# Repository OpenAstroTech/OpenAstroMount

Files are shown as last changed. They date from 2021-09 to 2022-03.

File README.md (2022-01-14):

# OpenAstroMount

OAM

v1.0 released now! 

The OpenAstroMount is a mount meant for larger telescopes that the OpenAstroTracker can't handle. It's fairly heavy and bulky, but can pack quite some payload. It features build in autoPA through motorized ALT and AZ axis. Both RA and DEC are driven entirely by belts, resulting in extremely low backlash. On both axis there is a two-stage belted gearbox with a reduction of 9:1 which, in combination with the large RA and DEC wheels, gives a total reduction of 316:1 and 234:1 for RA and DEC respectively. 

Specs:

| Weight | Cost | Payload | Performance (PHD2) |
|---|---|---|---|
| 12kg + tripod <br>& counterweights | ~300-500$ | 5+ kg* | 0.5-0.7" RMS |

`* since my heaviest gear weighs only about 4kg, i haven't tested the mount with more payload, hence the official payload recommendation remains 5kg. This will likely increase once the mount has been tested with more payload. ` 

---
### ToDo
- ~~AZ fine adjustment~~
- ~~ALT fine adjustment~~
- ~~RA/DEC gearboxes~~
- ~~cable managment~~
- ~~Place for MKS~~
- ~~Full BOM~~
- Guides
- Drill jigs

---
### Fix
- Misumi style extrusions do not fit parts
- ~~resize some holes~~
- ~~Base still too wobbly~~
- ~~RA Ring not printable on small printers~~
- ~~Some screws are very hard to reach~~
---
### Links
- [Guides](https://wiki.openastrotech.com/en/OpenAstroMount)
- [Shopping List](https://docs.google.com/spreadsheets/d/11bVmNJqMsgxGibqhDkgMZYvdXtIfOjpVwsbMoQk8eRM/edit?usp=sharing)
- [Printed parts list](https://docs.google.com/spreadsheets/d/1Y-b5y6xR6_xKHy6ZGzY7_cjVsc-U0AEJJASNaPWRuvU/edit?usp=sharing)

---
### Changelog:

see [changelog](https://github.com/OpenAstroTech/OpenAstroMount/blob/master/changelog.md)

---

<br /> <a href="https://github.com/OpenAstroTech/OpenAstroMount"> OpenAstroMount </a> &copy; 2021 by <a href="https://github.com/OpenAstroTech">OpenAstroTech </a> is licenced under <a rel="license" href="http://creativecommons.org/licenses/by-nc/4.0/">CC BY-NC 4.0</a>.

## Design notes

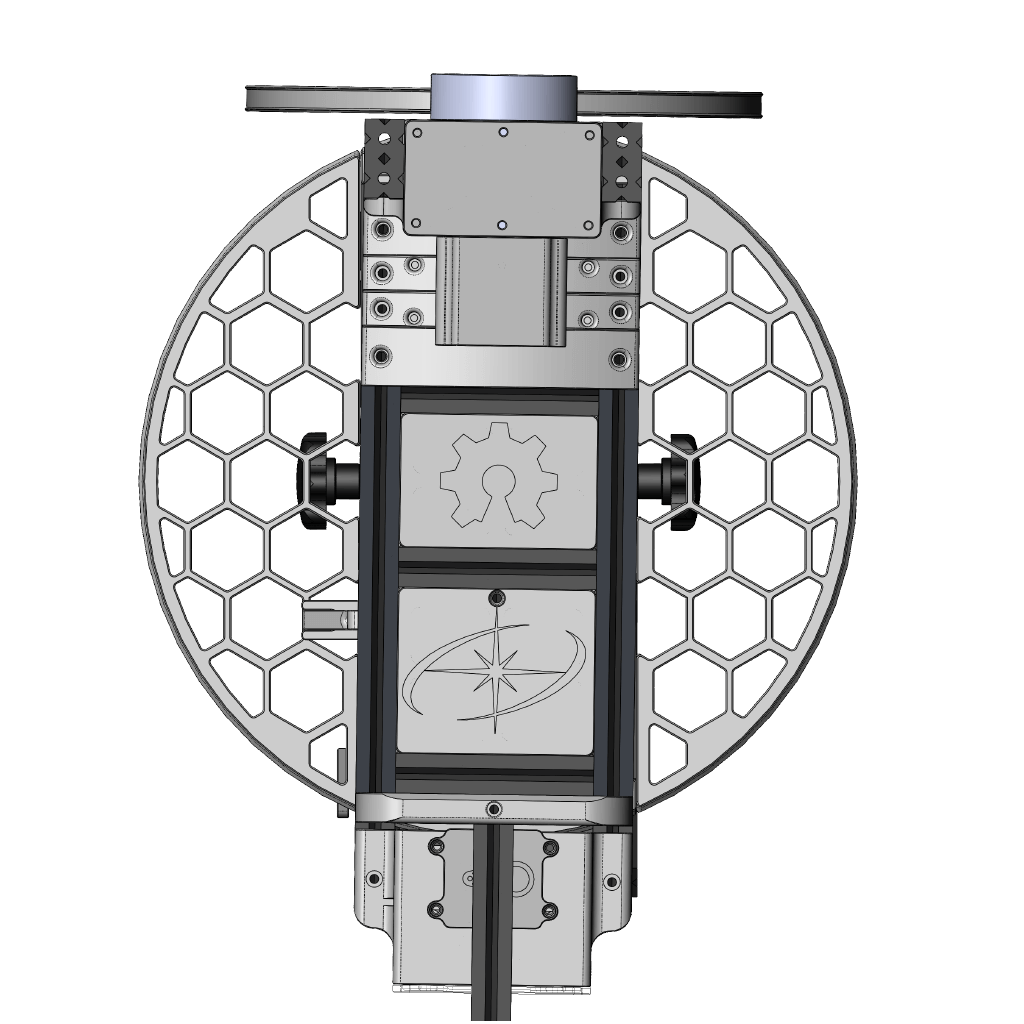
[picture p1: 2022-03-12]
CAD/Solidworks/OpenAstroMount_v1.0.PNG

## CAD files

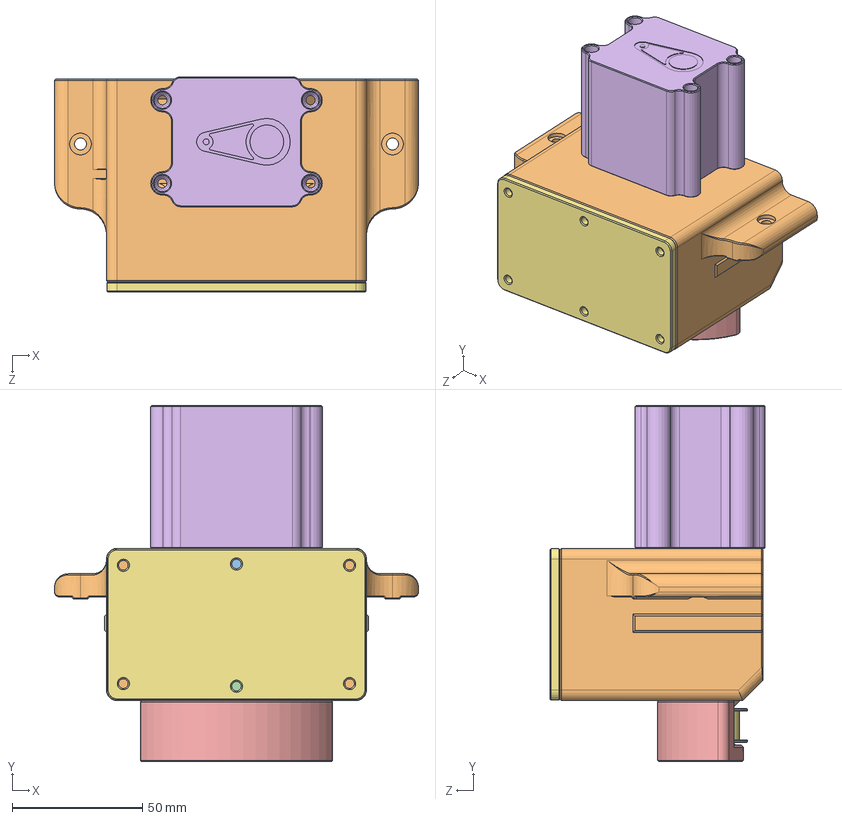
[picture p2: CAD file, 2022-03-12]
CAD/Solidworks/top_assembly/gearbox_v2/Gearbox_v2.SLDASM
140.0 x 137.0 x 82.8 mm
NEMA 17
GT2_16T x 2
GT2_16T_9mm
5x50mm rod x 2
625_bearing x 4
GT2_48T_8_6 x 2
GT2_idler_20T_toothless x 2
M5x30mm x 2
M5_nut x 2
gearbox_body_v2
Slider_top
Slider_bottom
pulley_cover
Stepper_cover
Lid

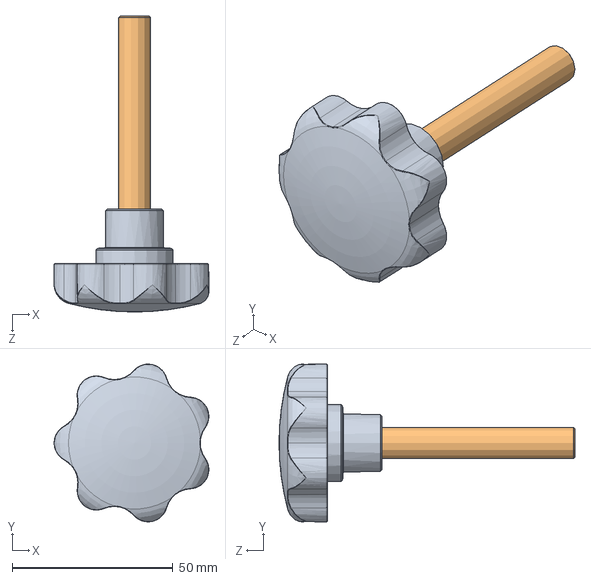
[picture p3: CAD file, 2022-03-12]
CAD/Solidworks/base_assembly/assembly_only/Star handle.stp.SLDASM
48.1 x 49.0 x 92.0 mm
Handle.stp
Bolt.stp

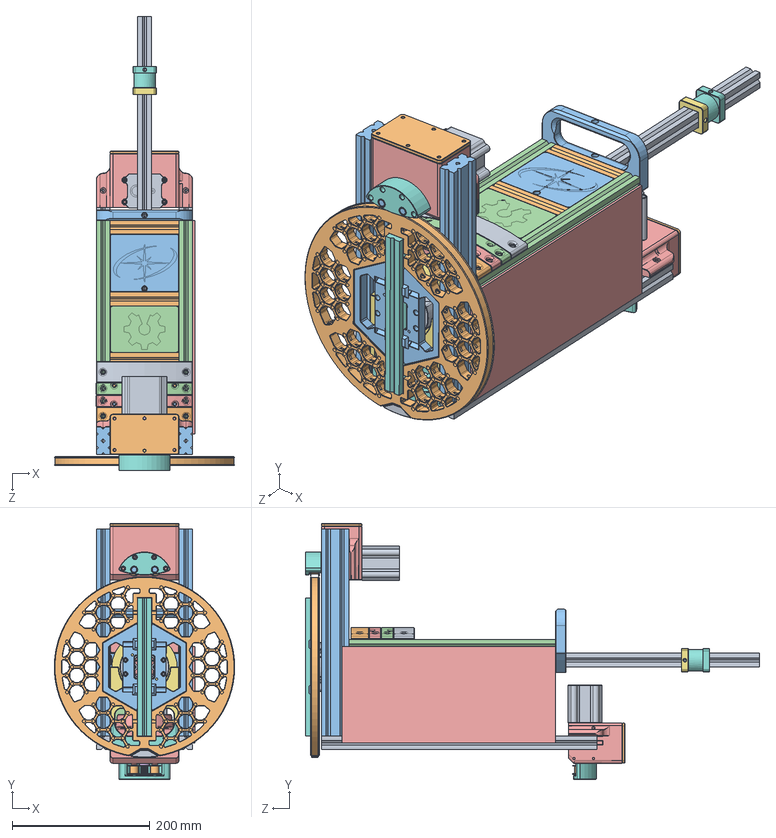
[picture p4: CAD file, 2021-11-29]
CAD/Solidworks/top_assembly/Top_Assembly.SLDASM
261.8 x 371.5 x 659.2 mm
2040 300mm x 2
Mancal F206 x 2
Rolamento UC206 x 2
6012 bearing x 2
4040_dual_slot
DEC_bearingHolder_rear_bottom
DEC_bearingHolder_front_bottom
DEC_bearingHolder_rear_top
DEC_bearingHolder_front_top
DECholder_1_v2
DECholder_2_v2
Baseplate_1_v1
top_cover
top_cover_2
Top_Plate_1
Top_Plate_2
MKS_enclosure
20x80x120
4040adapter_mid x 2
4040adapter_rear
4040adapter_front
DEC_wheel_2_v2
CW_2020_attachment_v2
NEMA 17 x 2
GT2_16T x 4
GT2_16T_9mm x 2
5x50mm rod x 4
625_bearing x 8
GT2_48T_8_6 x 4
GT2_idler_20T_toothless x 4
M5x30mm x 4
M5_nut x 4
gearbox_body_v2 x 2
Slider_top x 2
Slider_bottom x 2
pulley_cover x 2
Stepper_cover x 2
Lid x 2
DEC_wheel_1_v4 x 2
MKS_lid
UCF206_M5_adapter
CW_attachment_retainer
CW_attachment_31.5mm
Belt_retainer

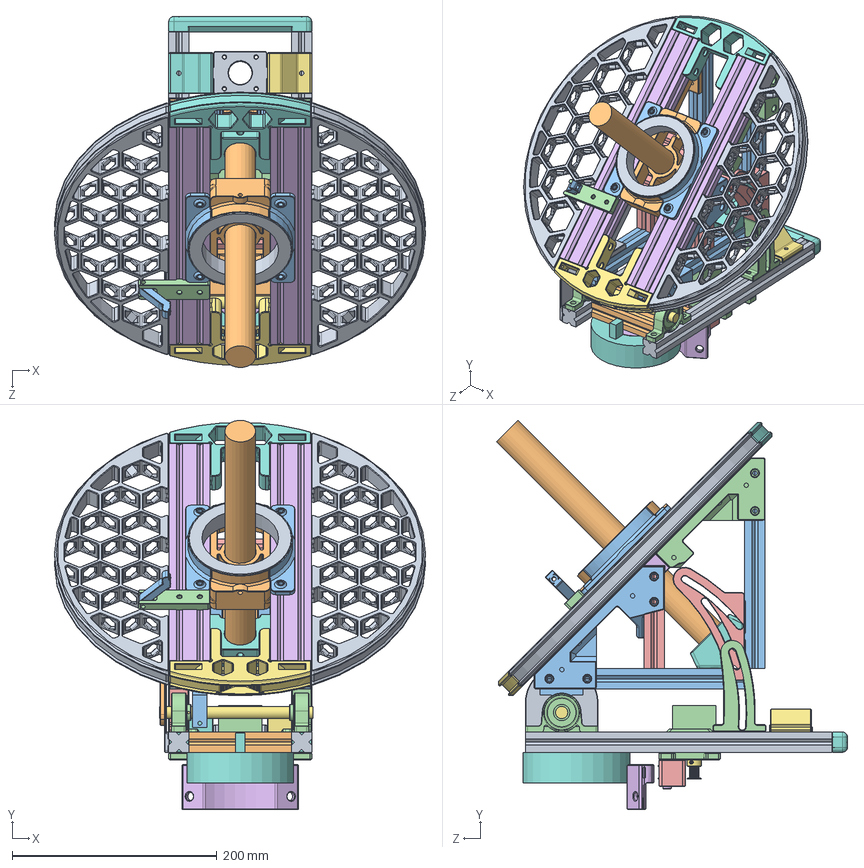
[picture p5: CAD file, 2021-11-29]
CAD/Solidworks/base_assembly/base_assembly.SLDASM
362.9 x 380.7 x 343.2 mm
2060_extrusion
KP001_D12 x 2
2040 300mm x 2
12x150mm_shaft
Tripod Base
51115 bearing
stahlstange 30mm
SK12 SHAFT HOLDER
NEMA 17
GT2_idler_20T_toothless
M5x30mm
GT2_16T_9mm
30mm_bracket_v2
base_connector_1.1_v2
base_connector_2.2
base_connector_1.2_v2
base_connector_2.1
30mm_pole_holder_1_v2
30mm_pole_holder_2_v2
RA_Ring_3
RA_Ring_2
RA_Ring_1_v2 x 2
51115_bearing_holder
51115_cover x 2
ALT_fastener_left_v2
ALT_fastener_right_v2
Tripod_adapter_v2
ALT_holder_left
ALT_holder_right
ALT_MotorHolder_v2
ALT_top
ALT_Top_2 x 2
AZ_motor_mount
AZ_idler_mount
AZ_tripod_adapter_EQ5
AZ_idler_distancer
rear_handle
ALT_clock
ALT_indicator
Parkingbreak_2
Parkingbreak_1

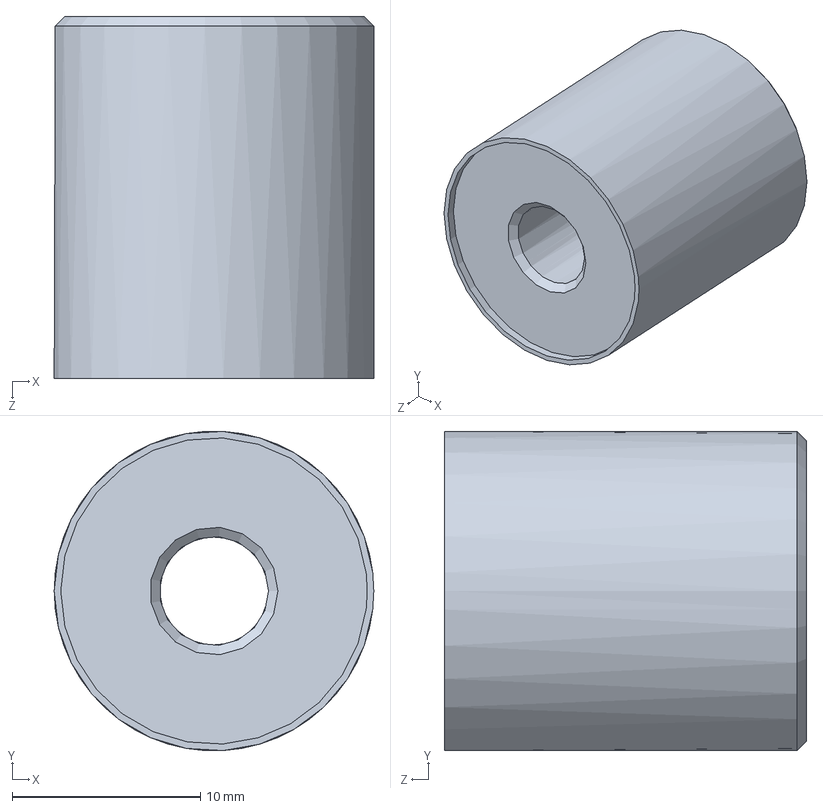
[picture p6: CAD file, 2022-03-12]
CAD/Solidworks/assembly_helpers/Bearing_insert_helper.SLDPRT
17.0 x 17.0 x 19.2 mm

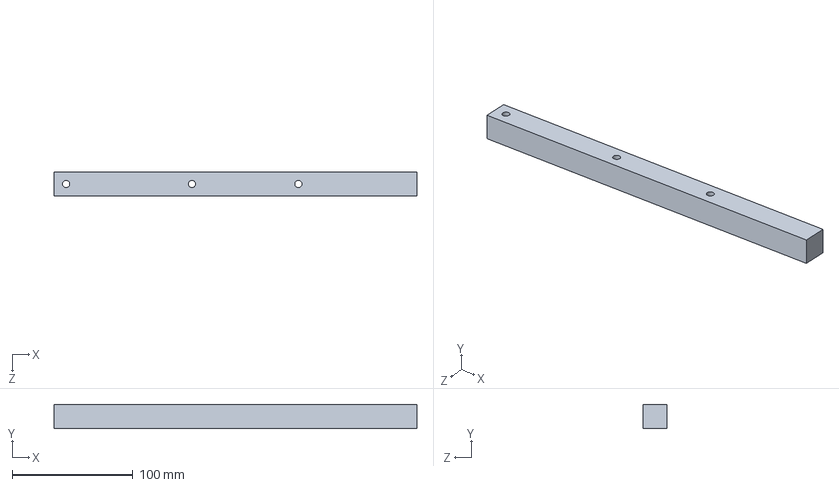
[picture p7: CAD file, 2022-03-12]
CAD/Solidworks/assembly_helpers/Drill_alignment/300mm_top_top.SLDPRT
300.0 x 20.0 x 20.0 mm

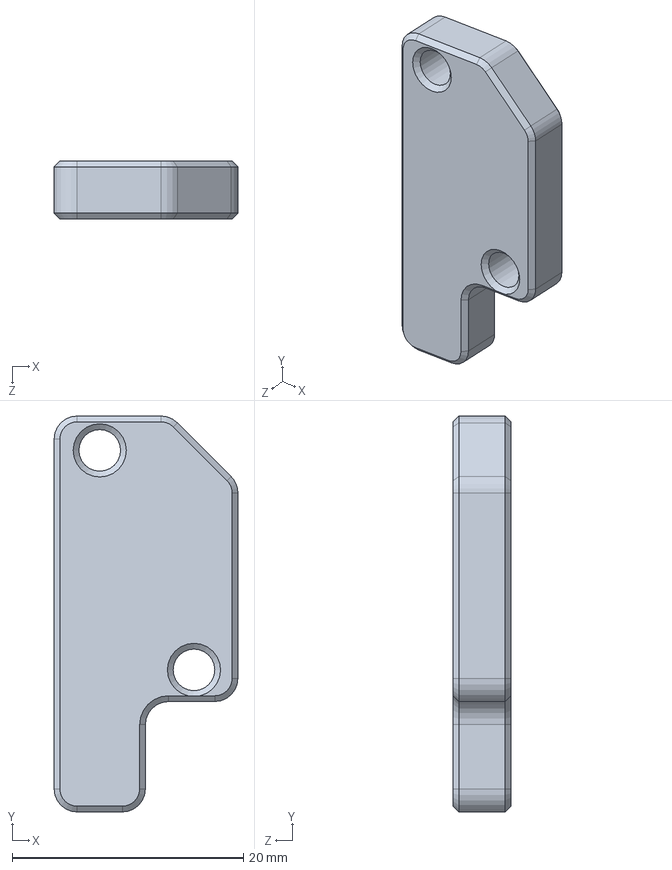
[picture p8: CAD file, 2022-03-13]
CAD/Solidworks/base_assembly/ALT_adjustment/ALT_bearing_lid_left.SLDPRT
15.9 x 34.2 x 5.00 mm

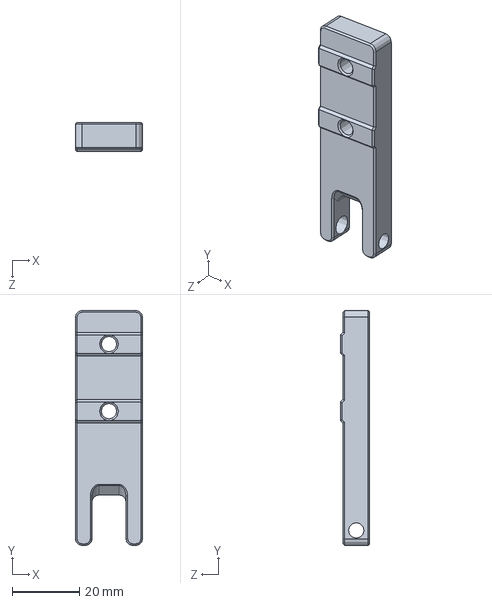
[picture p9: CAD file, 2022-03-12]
CAD/Solidworks/base_assembly/Parkingbreak_1.SLDPRT
20.0 x 70.0 x 8.75 mm

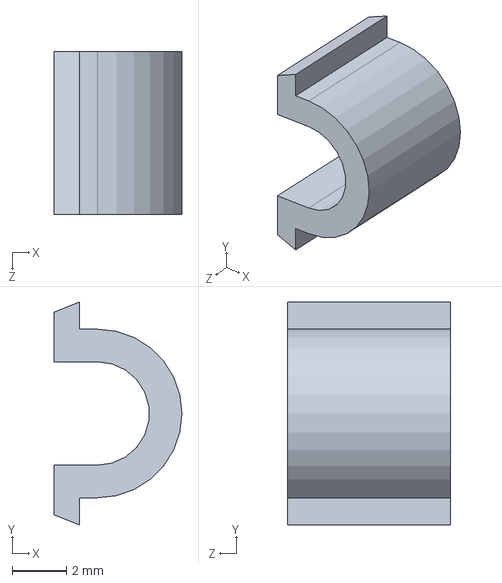
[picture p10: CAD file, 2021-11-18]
CAD/Solidworks/Cable_clip.SLDPRT
4.70 x 8.20 x 6.00 mm

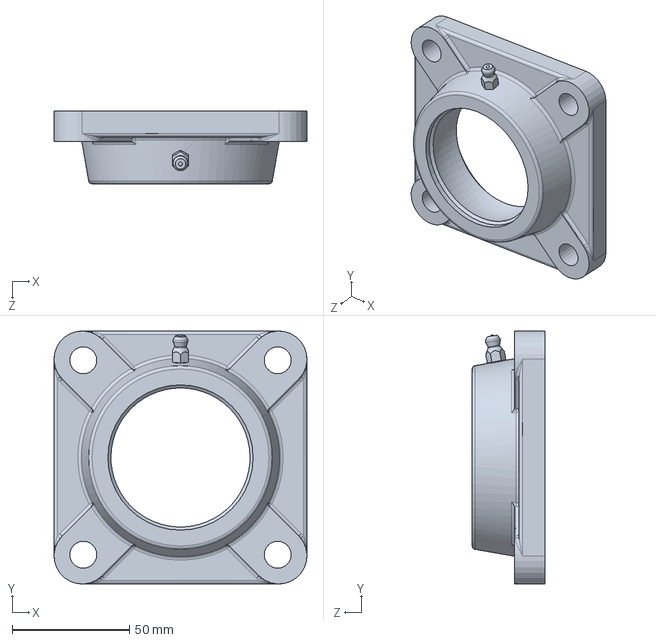
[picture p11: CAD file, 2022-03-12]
CAD/Solidworks/top_assembly/assembly_only/Mancal F206.SLDPRT
108.0 x 108.0 x 31.0 mm

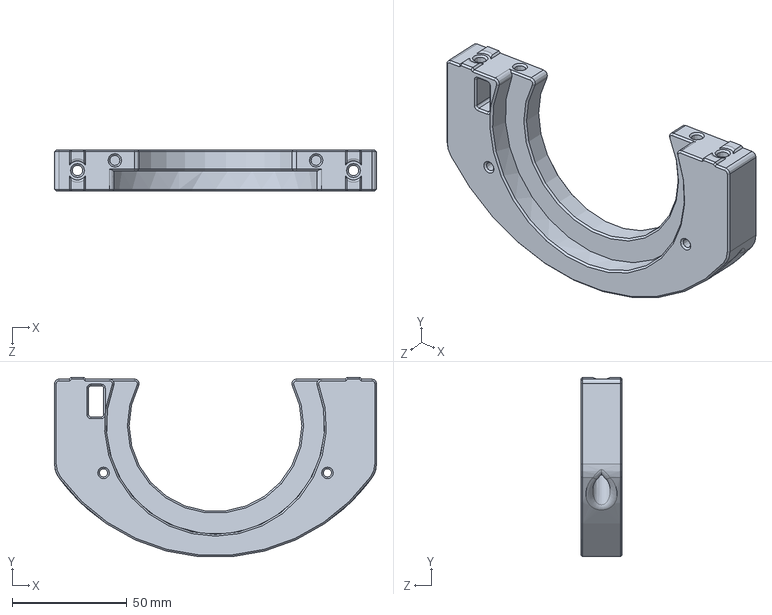
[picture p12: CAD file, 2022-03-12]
CAD/Solidworks/top_assembly/DEC_bearingHolder_rear_bottom.SLDPRT
140.0 x 78.0 x 18.0 mm

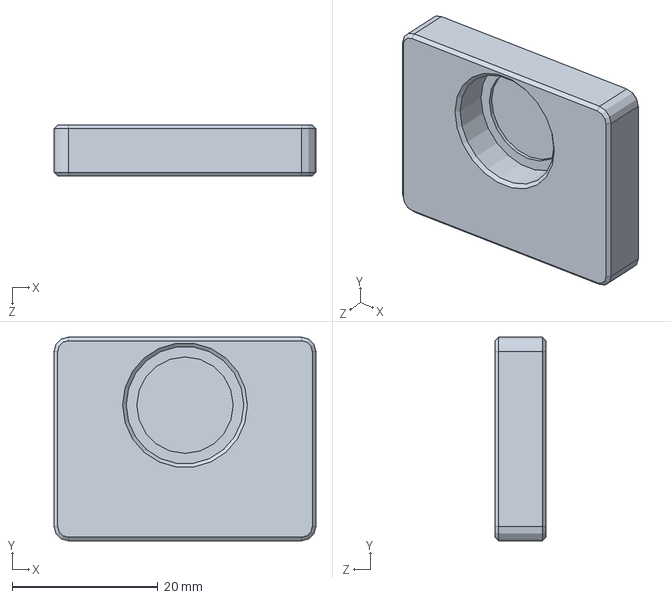
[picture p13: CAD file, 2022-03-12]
CAD/Solidworks/top_assembly/gearbox_v2/Slider_bottom.SLDPRT
36.0 x 28.0 x 7.00 mm

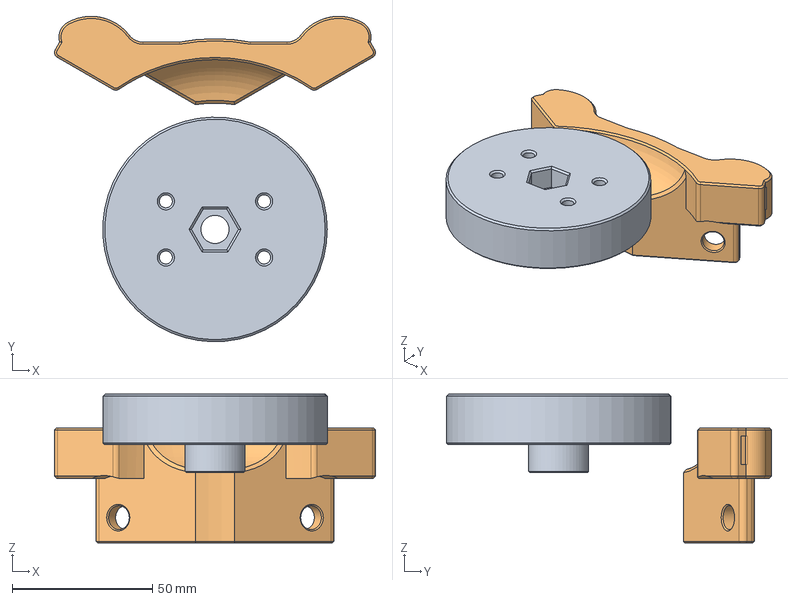
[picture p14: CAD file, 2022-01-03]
CAD/STEP/Meade_Tripod_mod_v1.step
114.3 x 115.9 x 53.0 mm
Tripod_adapter_Meade_v1
AZ_tripod_adapter_Meade

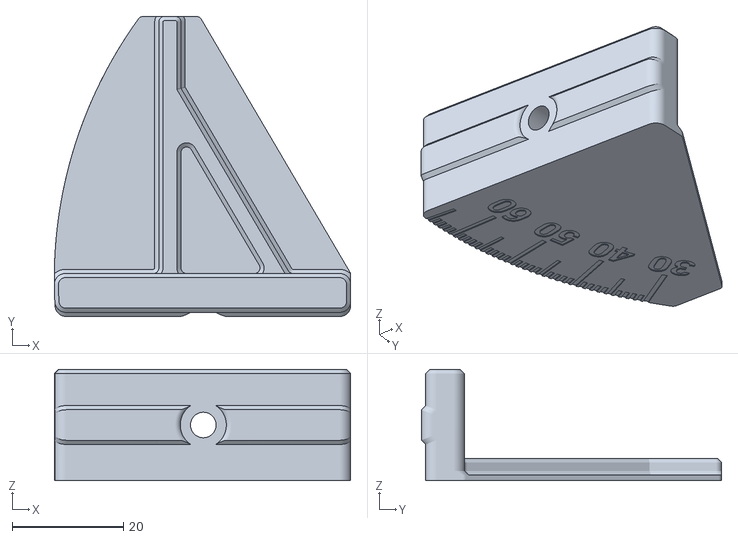
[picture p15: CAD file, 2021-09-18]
STL/ALT_clock.STL
53.4 x 54.0 x 20.0

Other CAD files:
STL/base_assembly/ALT-AZ_adjustment/ALT_bearing_lid_right.STL
STL/base_assembly/Tripod_adapter_EQ5_2_v2.STL
STL/top_assembly/CW_attachment_2inch.STL
CAD/Solidworks/assembly_helpers/Drill_alignment.SLDPRT
CAD/Solidworks/assembly_helpers/Drill_alignment/200mm_DEC.SLDPRT
CAD/Solidworks/assembly_helpers/Drill_alignment/200mm_base.SLDPRT
CAD/Solidworks/assembly_helpers/Drill_alignment/300mm_2040_top.SLDPRT
CAD/Solidworks/assembly_helpers/Drill_alignment/300mm_Base.SLDPRT
CAD/Solidworks/assembly_helpers/Drill_alignment/400mm_top_bottom.SLDPRT
CAD/Solidworks/assembly_helpers/Drill_alignment/Drawing.SLDDRW
CAD/Solidworks/assembly_helpers/Drill_alignment/Drill_alignment_1.SLDDRW
CAD/Solidworks/assembly_helpers/Drill_alignment/Drill_alignment_2.SLDDRW
CAD/Solidworks/base_assembly/30mm_bracket_v2.SLDPRT
CAD/Solidworks/base_assembly/30mm_pole_holder_1_v2.SLDPRT
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

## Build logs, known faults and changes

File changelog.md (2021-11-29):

**29.11.2021**
- v1.0 release
- nicer printed parts list
- added split RA Ring for smaller printer. 
- added MKS enclosure
- reworked entire base
- reworked DEC wheel
- reworked gearboxes
- change to 9mm belts for RA and DEC
- changed tripod adaption to a 2060 extrusion
- change to dual slot 4040 for DEC
- enforce blind joints for DEC and tripod adaption. Other blind joints are still optional
- various small things here and there

**18.11.2021**
- OAM v0.9 CAD upload
- deleted all STL's for reupload

**18.09.2021**
- updated Top_plate_1 and CW_2020_attachment_1 (now CW_2020_attachment) for more convenient CW bar attachment. Also added a handle for carrying to CW_2020_attachment.
- removed CW_2020_attachment_2 for redundancy 
- new part "30mm_bracket". Replaces "base_bracket_2 and _4" 
- new part "front_handle"
- new parts "ALT_clock" and "ALT_indicator" 
Added ALT motorisation:
- ALT_holder_1.1 & 1.2
- ALT_bearing_lid_1.1 & 1.2
- ALT_MotorMount
- ALT_Top_1 & 2

**24.07.2021**
- Make 'DEC_scope_attachment' significantly less wobbly
- add holes to 'DECholder' and 'DEC_bearingHolder' for easier assembly
- bigger hole in '4040adatper' for larger cables/plugs

**27.06.2021**
- initial CAD upload

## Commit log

2021-06-27 v0.1 initial CAD upload
    [1.SLDPRT, 200mm_stange.SLDPRT, 2020 100.SLDPRT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]
2021-07-07 add STL
    [2020_corner_adapter.STL, 30mm_pole_holder_1.SLDPRT, 30mm_pole_holder_1.STL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]
2021-07-24 Parts update - DEC
    - Make 'DEC_scope_attachment' significantly less wobbly
    - add holes to 'DECholder' and 'DEC_bearingHolder' for easier assembly
    - bigger hole in '4040adatper' for larger cables/plugs
    [4040adapter_1.1.SLDPRT, 4040adapter_1.2.SLDPRT, 4040adapter_1.2_alt.SLDPRT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]
2021-08-19 Add UCF206_adapter
    [UCF206_M5_adapter.STL]
2021-09-18 updates 18.09.2021
    see changelog
    [2020 100.SLDPRT, 20x80x120.SLDPRT, 20x80x120_MKS.SLDPRT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]
2021-09-18 fix ALT_clock
    [30mm_bracket.SLDPRT, ALT_Top_2.SLDPRT, ALT_bearing_lid_1.1.SLDPRT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]
2021-11-18 OAM v0.9 CAD upload
    ['_4040VÌý·_ÑOB4040V (1).SLDPRT, 1.SLDPRT, 12x150mm_shaft.SLDPRT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]
2021-11-23 OpenAstroMount v0.9
    - added STLs
    ['_4040VÌý·_ÑOB4040V (1).SLDPRT, 30mm_pole_holder_1_v2.STL, 30mm_pole_holder_2_v2.STL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]
2021-11-28 OAM v0.9.1
    [ALT_Top_2.SLDPRT, ALT_fastener_left_0-45deg.SLDPRT, ALT_fastener_right_0-45deg.SLDPRT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]
2021-11-28 OAM v0.9.2
    [20x80x120.SLDPRT, 20x80x120_MKS.SLDPRT, ALT_MotorHolder_v2.SLDPRT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]
2021-11-29 OAM v1.0 release
    [Belt_retainer.SLDPRT, Belt_retainer.STL, Frame_bracing_left.SLDPRT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]
2021-12-08 add alignment helper to 51115_bearing_holder
    [2040 300mm.SLDPRT, 30mm_pole_holder_1_v2.SLDPRT, 30mm_pole_holder_2_v2.SLDPRT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]
2021-12-18 add missing part Baseplate_2
    [Baseplate_2.SLDPRT, Baseplate_2.STL]
2022-01-02 Add Meade style tripod mount/adapter
    Adds the components needed to mount the OAM to a Meade style tripod.
    [Meade_Tripod_mod_v1.step]
2022-01-02 Added AZ tripod adapter for Meade style tripod
    AZ Tripod Adapter modified to work with a Meade style tripod.
    [AZ_tripod_adapter_Meade_v1.stl]
2022-01-02 Added Tripod adapter for Meade style tripod
    Tripod adapter modified to work with a Meade style tripod.
    [Meade_Tripod_mod_v1.step]
2022-01-02 Added Tripod adapter for Meade style tripod
    Tripod adapter modified to fit a Meade style tripod
    [Tripod_adapter_Meade_v1.stl]
2022-01-03 rename Tripod adapter EQ5
    [Tripod_adapter_1_v2.STL, Tripod_adapter_2_v2.STL, Tripod_adapter_EQ5_1_v2.STL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]
2022-03-12 add Drill Jig
    [Drill_alignment.SLDPRT, Drill_alignment.STL]
2022-03-12 updates
    Various small things
    [200mm_DEC.SLDPRT, 200mm_base.SLDPRT, 2020 100.SLDPRT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]
2022-03-13 add missing parts ALT_bearing_lid left&right
    [ALT_bearing_lid_1.1.SLDPRT, ALT_bearing_lid_1.2.SLDPRT, ALT_bearing_lid_left.SLDPRT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]
